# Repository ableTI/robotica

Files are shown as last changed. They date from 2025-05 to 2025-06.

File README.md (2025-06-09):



# About
This is the repository for all the files associated with, and used to create, a soccer robot for participation in the [Robocup](https://www.robocup.org/leagues/18). Made by students of the Mendelcollege, from team 'Mendel'. Our team consists of: Abel, Jits, Jorn, Lucas, Nathanaël, Ruben and Robin.

We will be participating in the Robocup Junior Soccer Lightweight 2:2. 2 Robots will play against 2 others on a field that resembles a human soccer field while both teams try to score in the opponents goal. There will be 2 rounds, each round will last 10 minutes with a 5 minutes break in between. One may only win with a 10 point difference or when at the end of the match they have more points. There will be a coin toss at the start of the game that will decide who can choose to either kick to ball or choose wich end the ball gets kicked to. The team that looses the coin toss gets the other option.
  
This is the Soccer Field. Official picture from the RoboCupJunior website.


This is our 3D model for our robot that will be playing soccer. It is made in Fusion by Nathanaël, Jorn and Jits. 


# Info:

  [Mendelcollege.nl](https://mendelcollege.nl/ontdek-je-talenten/robotica-en-beta/)

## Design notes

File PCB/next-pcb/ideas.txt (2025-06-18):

-ws2812B LED's for easyer full controll via a single signal
--using atmega8 controllers that relay data to teensy for all GPIO using devices for easier progaming.
--relay short circuit protection
--intergrated power level messurement (max17263xxTE)
--Distance sensors to not bumb into other robot's/walls
--multicore master controller not single core teensy (P8X32A-D40)
--use PWM capable pins to output PWM

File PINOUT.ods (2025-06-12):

pin | PAD_ID | Usage(Zephyr) | Actual_use | Name_Zephyr
0 | AD_B0_03 | GPIO1_3 / UART6_RX / CAN2_RX | UART-OpenMV
1 | AD_B0_02 | GPIO1_2 / UART6_TX / CAN2_TX | UART-OpenMV
2 | EMC_04 | GPIO4_4 | Soft_Power_Switch
3 | EMC_05 | GPIO4_5 | Driver3_PWM1
4 | EMC_06 | GPIO4_6 | Driver3_PWM2
5 | EMC_08 | GPIO4_8 | Driver3_enB
6 | B0_10 | GPIO2_10 | Driver3_enA
7 | B1_10 | GPIO2_17 / UART4_RX | UART-XIAO
8 | B1_01 | GPIO2_16 / UART4_TX | UART-XIAO
9 | B1_00 | GPIO2_11 | Driver2_PWM1
10 | B0_00 | GPIO2_0 | Driver2_PWM2
11 | B0_02 | GPIO2_2 | Driver2_enB
12 | B0_01 | GPIO2_1 | Driver2_enA
13 | B0_03 | GPIO2_3 / LED | PhotoResistor1
14 | AD_B1_02 | GPIO1_18 / UART2_TX | UART-XIAO
15 | AD_B1_03 | GPIO1_19 / UART2_RX | UART-XIAO
16 | AD_B1_07 | GPIO1_23 / UART3_RX / I2C3_SCL | Blue_LED
17 | AD_B1_06 | GPIO1_22 / UART3_TX / I2C3_SDA | Solenoid_Relay
18 | AD_B1_01 | GPIO1_17 / I2C1_SDA | I2C-compas
19 | AD_B1_00 | GPIO1_16 / I2C1_SCL | I2C-compas
20 | AD_B1_10 | GPIO1_26 / UART8_TX | Solenoid_Relay
21 | AD_B1_11 | GPIO1_27 / UART8_RX | Switch
22 | AD_B1_08 | GPIO1_24 / CAN1_TX | Switch
23 | AD_B1_09 | GPIO1_25 / CAN1_RX | Encoder_B_Motor_1
24 | AD_B1_12 | GPIO1_12 / UART1_TX / I2C4_SCL | Driver1_PWM1
25 | AD_B1_13 | GPIO1_13 / UART1_RX / I2C4_SDA | Driver1_PWM2
26 | AD_B1_14 | GPIO1_30 / SPI3_MOSI | Driver1_enB
27 | AD_B1_15 | GPIO1_31 / SPI3_SCK | Driver1_enA
28 | EMC_32 | GPIO3_18 / UART7_RX | Encoder_A_Motor_1
29 | EMC_31 | GPIO4_31 / UART7_TX | Encoder_B_Motor_2
30 | EMC_37 | GPIO3_23 / CAN3_RX | Encoder_A_Motor_2
31 | EMC_36 | GPIO3_22 / CAN3_TX | Encoder_B_Motor_3
32 | B0_12 | GPIO2_12 | Encoder_A_Motor_3
33 | EMC_07 | GPIO4_7 | Green_LED
34 | B1_13 | GPIO2_29 / UART5_RX | Red_LED
35 | B1_12 | GPIO2_28 / UART5_TX | PhotoResistor8
36 | B1_02 | GPIO2_18 | PhotoResistor7
37 | B1_03 | GPIO2_19 | PhotoResistor6
38 | AD_B1_12 | GPIO1_28 / SPI3_CS | PhotoResistor5
39 | AD_B1_13 | GPIO1_29 / SPI3_MISO | PhotoResistor4
40 | AD_B1_04 | GPIO1_20 | PhotoResistor3
41 | AD_B1_05 | GPIO1_21 / UART3_RX | PhotoResistor2

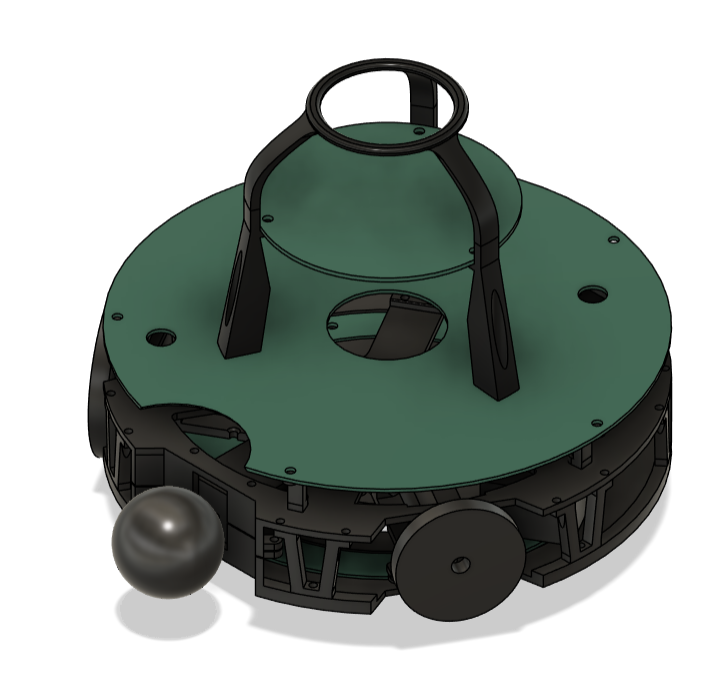
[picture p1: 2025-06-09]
3dfiles/Schermafbeelding 2025-06-04 153906.png

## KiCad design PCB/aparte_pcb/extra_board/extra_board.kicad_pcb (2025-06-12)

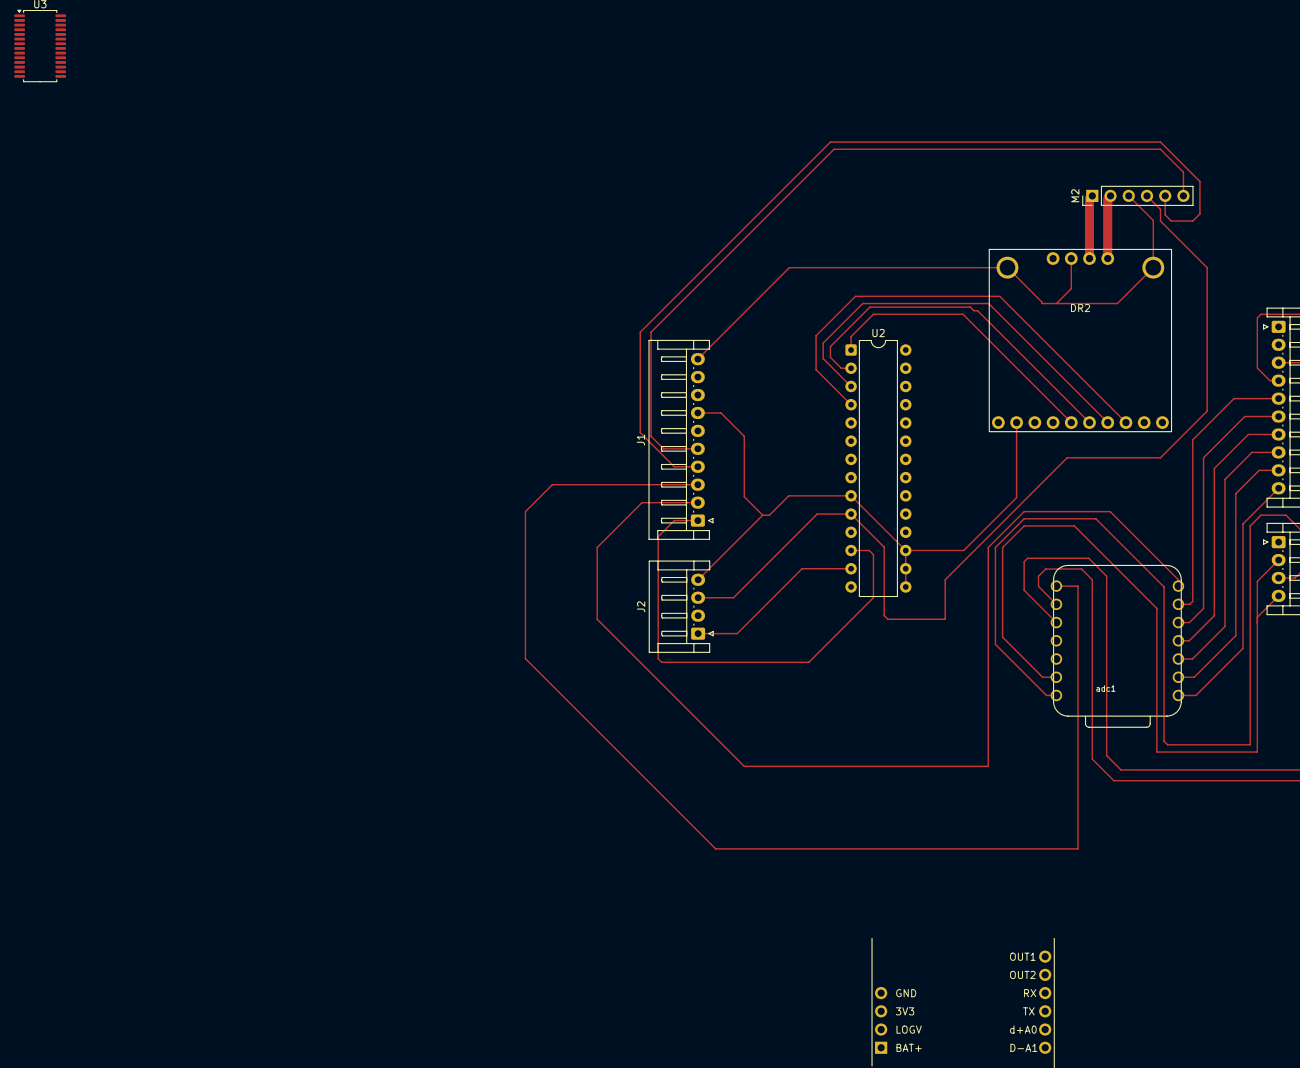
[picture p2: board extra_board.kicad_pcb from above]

Board: 2 copper layers, 10 parts (0 on the bottom side), 30 nets.

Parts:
DR2: motordriver
J1, J3: Conn_01x10_Pin; JST_EH_S10B-EH_1x10_P2.50mm_Horizontal
J2, J4: Conn_01x04_Pin; JST_EH_S4B-EH_1x04_P2.50mm_Horizontal
M2: PinHeader_1x06_P2.54mm_Vertical
U1: soccer communinication module; soccer-communication-module
U2: MCP23017_SP; DIP-28_W7.62mm
U3: PCA9685PW; TSSOP-28_4.4x9.7mm_P0.65mm
adc1: Seeed Studio XIAO SAMD21; XIAO-SAMD21-SMD

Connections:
+5V: J2.3, J4.3, M2.4 (Vcc), U1.2 (logv), U3.14 (VSS), U3.25 (EXTCLK)
+12V: DR2.1 (VIN), U1.1 (BAt+)
/BLUE: J4.1, U3.12 (LED6)
/D+A0: J1.3, U1.6 (d+a0)
/D-A1: J1.2, U1.5 (d-a1)
/GREEN: J3.1, U3.11 (LED5)
/OUT1: J1.4, U1.10 (OUT1)
/OUT2: J1.5, U1.9 (OUT2)
/RED: J3.2, U3.10 (LED4)
/RX: J1.9, adc1.7 (PB08_A6_D6_TX)
/SCL: J1.10, U3.26 (SCL)
/SDA: J2.1, U3.27 (SDA)
/TX: J1.8, adc1.8 (PB09_A7_D7_RX)
/encA: J1.6, M2.5 (A_out)
/encB: J1.7, M2.6 (B_out)
/pr1: J3.10, adc1.1 (PA02_A0_D0)
/pr2: J3.9, adc1.2 (PA4_A1_D1)
/pr3: J3.8, adc1.3 (PA10_A2_D2)
/pr4: J3.7, adc1.4 (PA11_A3_D3)
/pr5: J3.6, adc1.5 (PA8_A4_D4_SDA)
/pr6: J3.5, adc1.6 (PA9_A5_D5_SCL)
/pr7: J3.4, adc1.9 (PA7_A8_D8_SCK)
/pr8: J3.3, adc1.10 (PA5_A9_D9_MISO)
GND: DR2.0 (screw), DR2.2 (GND), DR2.6 (GND), J1.1, J2.2, J2.4, J4.2, J4.4, M2.3 (GND), U1.4 (gnd), U2.9 (VDD), U2.15 (A0), U2.16 (A1), U2.17 (A2), U3.1 (A0), U3.2 (A1), U3.3 (A2), U3.4 (A3), U3.5 (A4), U3.22 (LED15), U3.24 (A5), U3.28 (VDD), adc1.13 (GND)
unnamed: DR2.9 (EN), U2.1 (GPB0), U3.6 (LED0)
unnamed: DR2.10 (ENB), U2.2 (GPB1), U3.7 (LED1)
unnamed: DR2.4 (OUT1), M2.2 (MotorPW)
unnamed: DR2.3 (OUT2), M2.1 (MotorPW)
unnamed: DR2.12 (PWM1), U2.4 (GPB3), U3.9 (LED3)
unnamed: DR2.11 (PWM2), U2.3 (GPB2), U3.8 (LED2)

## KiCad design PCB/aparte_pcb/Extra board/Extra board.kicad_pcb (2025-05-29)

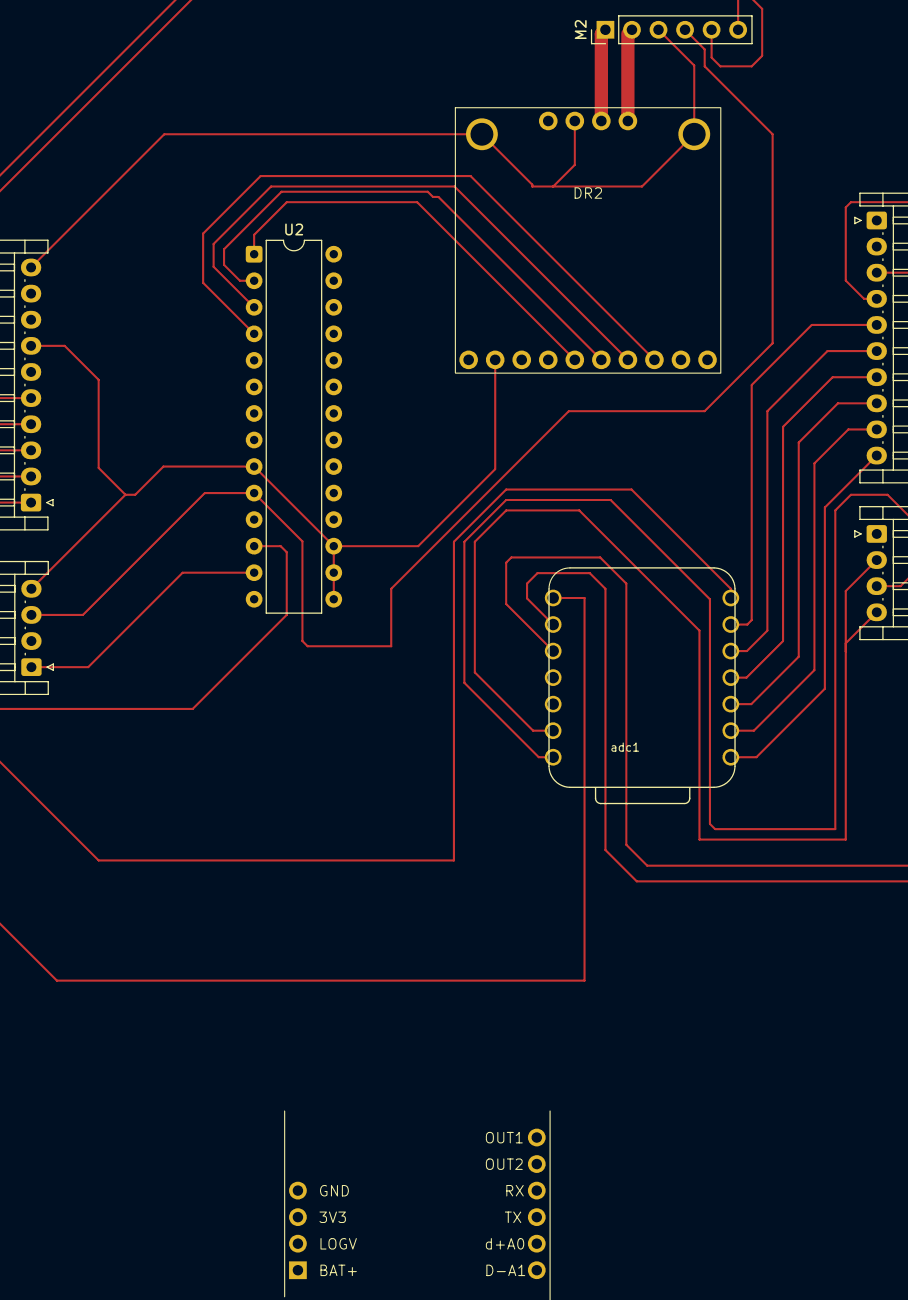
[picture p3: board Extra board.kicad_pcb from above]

Board: 2 copper layers, 9 parts (0 on the bottom side), 25 nets.

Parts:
DR2: motordriver
J1, J3: Conn_01x10_Pin; JST_EH_S10B-EH_1x10_P2.50mm_Horizontal
J2, J4: Conn_01x04_Pin; JST_EH_S4B-EH_1x04_P2.50mm_Horizontal
M2: PinHeader_1x06_P2.54mm_Vertical
U1: soccer-communication-module
U2: MCP23017_SP; DIP-28_W7.62mm
adc1: Seeed Studio XIAO SAMD21; XIAO-SAMD21-SMD

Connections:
5v: J2.3, J4.3, M2.4 (Vcc), U1.2 (logv), U2.10 (VSS), adc1.14 (5V)
D+A0: J1.7, U1.6 (d+a0)
D-A1: J1.8, U1.5 (d-a1)
GND: DR2.0 (screw), DR2.2 (GND), DR2.6 (GND), J1.9, J1.10, J2.2, J2.4, J4.2, J4.4, M2.3 (GND), U1.4 (gnd), U2.9 (VDD), U2.15 (A0), U2.16 (A1), U2.17 (A2), adc1.13 (GND)
unnamed: DR2.9 (EN), U2.1 (GPB0)
unnamed: DR2.10 (ENB), U2.2 (GPB1)
unnamed: DR2.4 (OUT1), M2.2 (MotorPW)
unnamed: DR2.3 (OUT2), M2.1 (MotorPW)
unnamed: DR2.12 (PWM1), U2.4 (GPB3)
unnamed: DR2.11 (PWM2), U2.3 (GPB2)
OUT2: J1.6, U1.9 (OUT2)
RX: J1.2, adc1.7 (PB08_A6_D6_TX)
SCL: J1.1, U2.12 (SCK)
SDA: J2.1, U2.13 (SDA)
TX: J1.3, adc1.8 (PB09_A7_D7_RX)
encA: J1.4, M2.5 (A_out)
encB: J1.5, M2.6 (B_out)
pr1: J3.10, adc1.1 (PA02_A0_D0)
pr2: J3.9, adc1.2 (PA4_A1_D1)
pr3: J3.8, adc1.3 (PA10_A2_D2)
pr4: J3.7, adc1.4 (PA11_A3_D3)
pr5: J3.6, adc1.5 (PA8_A4_D4_SDA)
pr6: J3.5, adc1.6 (PA9_A5_D5_SCL)
pr7: J3.4, adc1.9 (PA7_A8_D8_SCK)
pr8: J3.3, adc1.10 (PA5_A9_D9_MISO)

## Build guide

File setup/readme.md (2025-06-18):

# Downloading
Download an debian testing live iso, i recomend the [Live Xfce ISO](https://cdimage.debian.org/cdimage/weekly-live-builds/amd64/iso-hybrid/debian-live-testing-amd64-xfce.iso) for it is the most lightweight of them.

# Flashing
Flash it using [Rufus] (https://rufus.ie/nl/). The default settings are mostly fine, but make shute the Persistent partition size is big enough, becouse that is where all you files will be stored. If it asks you to download somthing from the internet the anser is usualy yes..

# Booting
In order to boot the system you will need to turn of the device where you will run it on. After that you will need to go into you system's boot menu. For the laptops at school you will need to enter it with this [manual](https://support.lenovo.com/us/en/solutions/ht104668-how-to-select-boot-device-from-bios-boot-menu-ideapad-thinkpad-thinkstation-thinkcentre-ideacentre). If you want to do it via another device you will need to search for an manual yourself.

# Change password
In the terminal type *passwd* and follow the instructions

# Setup git
In order to use git you will need to configure an [GPG](https://docs.github.com/en/authentication/managing-commit-signature-verification/generating-a-new-gpg-key) and an [SSH](https://docs.github.com/en/authentication/connecting-to-github-with-ssh/generating-a-new-ssh-key-and-adding-it-to-the-ssh-agent) key. [DONT FORGET](https://docs.github.com/en/authentication/managing-commit-signature-verification/telling-git-about-your-signing-key) && [How to use git](https://education.github.com/git-cheat-sheet-education.pdf).
(SSH is blocked on the mendelnetwork so setup https auth via *gh auth*)

Configure the [commit template](https://git-scm.com/book/en/v2/Customizing-Git-Git-Configuration) *wget https://raw.githubusercontent.com/mendelcollege-robotics/robotica/refs/heads/main/setup/.gitmessage.txt -O ~/.gitmessage.txt && git config --global commit.template ~/.gitmessage.txt*

clone repo using *git clone repolink*

# Setup arduino 1.x
open a terminal and enter, 
*sudo apt install arduino*

# Setup arduino 2.x
1. Download the arduino install linux zip file on the [arduino website](https://www.arduino.cc/en/software/).

2. Extract it.

3. Place it into the /usr/share folder with the command *sudo mv /path/to/arduino-ide_2.X.X_Linux_64bit /usr/sharearduino-ide_2.X.X_Linux_64bit*

4. Create an .desktop file in /usr/share/applications/ called arduino2.desktop with [this](https://github.com/mendelcollege-robotics/robotica/blob/main/setup/arduino2.desktop) content by entering *sudo wget https://raw.githubusercontent.com/mendelcollege-robotics/robotica/refs/heads/main/setup/arduino2.desktop -O /usr/share/applications/arduino2.desktop*

5. Edit the file to your version with *sudo nano /usr/share/applications/arduino2.desktop*. To exit see help commands below (^ means ctrl).

# [Setup teensyduino](https://www.pjrc.com/teensy/td_download.html)

# [Setup arduino for Seeed Xiao](https://wiki.seeedstudio.com/Seeed_Arduino_Boards/)

# Setup KiCAD
open a terminal and enter, 
*sudo apt intall kicad*

# Setup OpenMV
Go to the [openMV website](https://openmv.io/pages/download) and download the ubuntu tar.gz and extract it. Run /path/to/openmv-ide/setup.sh

# Fussion 360
I am not sure if it works but there is [an way to make it work on linux](https://github.com/cryinkfly/Autodesk-Fusion-360-for-Linux) via [wine](https://www.winehq.org/).

# [Zephyr](https://docs.zephyrproject.org/latest/develop/getting_started/index.html)

# Usefull packages
in your terminal run: 
*sudo apt update && sudo apt install --no-install-recommends git cmake ninja-build gperf
  ccache dfu-util device-tree-compiler wget \
  python3-dev python3-pip python3-setuptools python3-tk python3-wheel xz-utils file \
  make gcc gcc-multilib g++-multilib libsdl2-dev libmagic1 \
  python3-venv putty supertuxkart thefuck sl inkscape blender \
  freecad kate vlc krita gnupg-utils micro nano cheese \
  kleopatra qbittorrent wireguard nmap usb-utils gparted*

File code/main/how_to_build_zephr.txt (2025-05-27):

https://docs.zephyrproject.org/latest/boards/pjrc/teensy4/doc/index.html
https://docs.zephyrproject.org/latest/develop/getting_started/index.html

replace /path/to/project/ with the actual path to you project

Create, configure and enter virtual enviorment
    python3 -m venv /path/to/project/.venv
    source /path/to/project/.venv/bin/activate
    pip install west
    west init /path/to/project/
    cd /path/to/project/
    west update
    west zephyr-export
    west packages pip --install

Install zephyr SDK
    cd /path/to/project/zephyr
    west sdk install

build project for teensy 4.1:
    west build -b teensy41 /path/to/project/

flash project onto the device:
    cd /path/to/project/
    west flash

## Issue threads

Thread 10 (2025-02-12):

coderen

robosoccer, 2025-02-12:

robosoccer, 2025-02-26:
1. Motor drivers -- on/off -- 6 direction drive
2. comm tussen seeed-teensy
3. Led's controll+ foto res
4. IR sens
5. Comp
6. Cam

Closed 2025-03-20.

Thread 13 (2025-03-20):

PWM

ableTI, 2025-03-20:
add speed regulation to motors

ableTI, 2025-03-20:
also works it code, need to test in reel

ableTI, 2025-03-21:
tested via multimeter, updated code and works

Closed 2025-03-21.

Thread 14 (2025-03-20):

line detection

ableTI, 2025-03-20:
The LED are emmiting red led, add code to see white lines and make the robot react to it

ableTI, 2025-03-20:
analog ports arent used, use on/off via selected resistor

ableTI, 2025-03-20:
need to test but code done

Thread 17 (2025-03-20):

isolatie IR signaal

ableTI, 2025-03-20:
Zorg dat het alleen signaalen van voor de sensor krijgt, nu krijgt het zowat rondom signaalen.
https://4donline.ihs.com/images/VipMasterIC/IC/VISH/VISH-S-A0007978048/VISH-S-A0007978048-1.pdf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

ableTI, 2025-03-20:
aluminium tape

Closed 2025-03-20.

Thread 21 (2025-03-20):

Betere motor controller

ableTI, 2025-03-20:
Gebruik rpm counter en volledige 360 graden richting

ableTI, 2025-03-22:
Fix PWM

robosoccer, 2025-04-01:
SoftPWM.h werkt niet, ga weer zelf schijfen maar nu beter

ableTI, 2025-04-24:
PID moet goed

robosoccer, 2025-06-02:
Create a functioning PID inhttps://github.com/mendelcollege-robotics/robotica/blob/main/code/debug/motors/with-pid/with-pid.ino

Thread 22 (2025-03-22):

Serial comm

ableTI, 2025-03-22:
-het duurt ~2,5s tot data tussen seeed en teensy gestuurd word.
-2 seeeds op verschillende lijnen komen samen in een teensy serial port, geen idee hoe.

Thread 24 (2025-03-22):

Onder pcb ruimte fixen

ableTI, 2025-03-22:

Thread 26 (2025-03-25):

nieuwe wielen + barrel jack oplader

Jorns57, 2025-03-25:
wielen met frank enzo

robosoccer, 2025-03-27:
ook een teensy en twee seeed xiao

robosoccer, 2025-03-27:
https://gtfrobots.com/product/50mm-diameter-4mm-hole-size-omni-wheel/           6x

robosoccer, 2025-03-27:
https://www.tinytronics.nl/en/development-boards/microcontroller-boards/others/seeed-studio-seeeduino-xiao-cortex-m0-samd21 2x                                             https://www.tinytronics.nl/en/development-boards/microcontroller-boards/teensy/teensy-4.1-without-ethernet

Jorns57, 2025-03-30:
Barreljack oplader -> Jorn neemt mee vanuit huis

Jorns57, 2025-04-03:
Do 11-04 : wielen uit elkaar halen -> kwaliteit bepalen

robosoccer, 2025-04-04:
teensy, seeed's en openMV kabel zijn binnen gekomen

Jorns57, 2025-04-06:
ik heb thuis de juiste set screws (m4*~5mm) voor de wielen, die hoeven we dus niet te bestellen

Closed 2025-04-10.

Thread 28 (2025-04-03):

EK praktisch

Jorns57, 2025-04-03:
https://www.icjapigia1verga.it/robocupjunior/

-> Website nog niet af. Dus prijzen, hotels, slots en exacte data nog onbekend
- Mails sturen naar oa voetbal@robocupjunior.nl en wellicht roboticus voor duidelijkheid slots

Alle kosten (waaronder toegankskosten) moeten wij zelf onderverdelen. Ik (Jorn) rijd naar Italië van te voren (voor eigen vakantie) met zo veel mogelijk spullen, dus dat hoeft niet mee het vliegtuig in (of het vervoersmiddel dat andere mensen gebruiken). Het EK is van 4-7 Juni (week 23, week na hemelvaart)

Jorns57, 2025-04-06:
de mail die ik donderdag verstuurd heb is nog onbeantwoord, hopelijk voor aankomende donderdag antwoord

Closed 2025-05-22.

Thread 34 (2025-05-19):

Camera

Nathan220806, 2025-05-19:

Nathan220806, 2025-05-19:
openmv h7

ableTI, 2025-05-20:
Camera heeft al een issue, 'goal detection'.

Closed 2025-05-20.

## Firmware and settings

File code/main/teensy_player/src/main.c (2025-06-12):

#include <zephyr/kernel.h>
#include <zephyr/device.h>
#include <zephyr/drivers/gpio.h>
#include <zephyr/sys/printk.h>
#include <zephyr/sys/__assert.h>
#include <zephyr/drivers/uart.h>
#include <zephyr/drivers/pwm.h>
#include <string.h>

/* Stack sizes (now only one size)*/
/* To figure out how much is necessary: */
/* https://zephyr-docs.listenai.com/guides/debug_tools/thread-analyzer.html */
#define GENERAL_THREAD_STACKSIZE 1024

/*the pinout configuration*/
/*https://docs.zephyrproject.org/latest/boards/pjrc/teensy4/doc/index.html*/
/*motors pins*/
#define m1enA DT_ALIAS(GPIO2_10)    /*pin 6*//*Motor 1 EN A*/
#define m1enB DT_ALIAS(GPIO4_8)     /*pin 5*//*Motor 1 EN B*/
#define m1pwm1 DT_ALIAS(GPIO4_6)    /*pin 4*/
#define m1pwm2 DT_ALIAS(GPIO4_5)    /*pin 3*/
/*encoder pins*/
#define m1encoA 32  /*pin 32   &&   encoder number 0*/
#define Nm1encoA INT_TO_POINTER(0)
#define m1encoB 31  /*pin 31   &&   encoder number 1*/
#define Nm1encoB INT_TO_POINTER(1)

/*set priorities*/
#define ENC_ISR_PRIO 1

/*encoders/PWM/PID*/
#define NUM_ENCODERS 2     /*how many encoder pins there are*/
volatile int encCount[NUM_ENCODERS] = {0};

/*misc*/
#define NO_IRQ_FLAGS 0
#define PWM_PERIOD_µS 1600   /*The lengt of an full PWM cycle in microseconds*/

void ENCO_ISR(void *encN){
    /*adds one to the encoder where a change of state is detected*/
    int encoder = (int)(intptr_t)encN;
    if (encoder >= 0 && encoder < NUM_ENCODERS) {
        encCount[encoder]++;
    }

}

void ENC_ISR_installer(void){
    /*sets up the interrupts for the encoder at same priority, need to configure FIFO in case of simultaneous call*/
    IRQ_CONNECT(m1encoA, ENC_ISR_PRIO, ENCO_ISR, '0', NO_IRQ_FLAGS);
    IRQ_CONNECT(m1encoB, ENC_ISR_PRIO, ENCO_ISR, '1', NO_IRQ_FLAGS);
}

int main(void){}

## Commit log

2025-05-26 extra PCB changes
    Multi-line description of commit,
    feel free to be detailed.
    [Extra board.kicad_sch, midden.kicad_sch]
2025-05-26 almost finished extra pcb
    The pcb is designed to be single layerd for simplisity, but there are still two unconnected lines, GND and 5V are now both in two seperate sections. Can connect via an wire or update the PCB. Will no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
    [Extra board.kicad_pcb, Extra board.kicad_sch, boven.kicad_sch]
2025-05-29 encoder zephyr
    Think this should work to use the encoder but cna only build not upload, need to wait till monday till i can test it with a robot.
2025-05-29 Communication module.
    Added Communication module to extra PCB, but the power requerments are either our battery power or 3v, but current lines only allow 5v, so either new lines or an power conversion component.
    Need to discuss best option with team.
    Also TX/RX lines optional but not available. I2C to UART module?
    Also need to discuss.
    [Extra board.kicad_pcb, Extra board.kicad_sch]
2025-06-04 multiple things
    [total.kicad_pcb, total.kicad_sch]
2025-06-09 Changes to PCB
    added some symboles did some changes.
    [total.kicad_sch, total_pcb.kicad_sch]
2025-06-12 recenltly removed three commit becouse it included files that shouldn't be included.
    Did reset hard,
    localy unstaged commits, deleted files and recommited the good files.
    think this is all i did since,
    -changed extra PCB name to bave and _ instead of a space so i dont have to use ""
    -added button and led to teensy41 goaly overlay
    -started on PWM, not complete
    Abel Tim <git@abeltim.com>
    [Extra board.kicad_sch, PINOUT.ods, extra_board.kicad_pcb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]
